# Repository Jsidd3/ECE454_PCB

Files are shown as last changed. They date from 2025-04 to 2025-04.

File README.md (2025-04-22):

# ECE454_PCB
PCB design files for UIC ECE 454 Team 6 Autonomous Race Car. PCB Designed by Jawwad Siddiqui

PCB will interface with the NXP FRDM-KL25Z board. Serves as the main power supply and motor controller for ECE 454 Team 6 Autonomous Race Car. Power supply consists of boost converter and linear regulator, and motor controller consists of FET Drivers. Current version is Rev. A.



Soldered using Voltera PCB Printer
WhatsApp Image 2025-04-14 at 16 43 18_f0a2d588
Designed using Altium Designer by Jawwad Siddiqui. Credit to Nico Gomez who also contributed to the Motor Controller Schematic.

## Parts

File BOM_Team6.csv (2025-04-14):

 | Bill of Materials
 |  |  |  |  |  |  | 2175 Salk Avenue
 | Project Title: | Bill of Materials for BOM Document [Motor_Controller_PowerSupply.BomDoc] |  |  |  |  | Suite 200
 | Project File Name: | Motor_Controller_PS.PrjPcb |  |  |  |  | Carlsbad, CA 92008
 | Assembly Variant: | None |  |  |  |  | USA
Part Number | Description | Designator | Manufacture | Manufacture Part Number | Supplier | Supplier Part Number | Supplier Unit Price | Quantity
DesignItemId | Description | Designator | Manufacturer 1 | Manufacturer Part Number 1 | Supplier 1 | Supplier Part Number 1 | Supplier Unit Price 1 | Quantity
LT1370CR#PBF | 12V Boost Converter | Boost Converter | Analog Devices / Linear Technology | LT1370CR#PBF | Digikey | 505-LT1370CR#PBF-ND | $19.50 | 1
CMP-2007-04425-2 | General Purpose Ceramic Capacitor, 0805, 47nF, 5%, X7R, 0.15, 50V | C1, C2 | Kyocera AVX | 08055C473JAT2A | Newark | 96M1415 | $0.03 | 2
2220Y2K00104KXRWS3 | Capacitor | C1Hall | Knowles Syfer | 2220Y1K00104KSTM01 | Digikey | 1608-2220Y1K00104KSTM01CT-ND | $4.02 | 1
C1812C472KGRACAUTO | Capacitor | C2Hall | KEMET | C1812C472KGRACAUTO | Digikey | 399-16791-1-ND | $0.78 | 1
CMP-03017-000047-1 | CAP TANT 1UF 10% 25V 1206 | C3 | KEMET | T491A105K025AT | Digikey | 399-3680-1-ND | $0.42 | 1
UWP1HR22MCL1GB | Capacitor Polarised | CL, Cp1, Cp4 | Nichicon | UWP1HR22MCL1GB | Digikey | 493-9831-1-ND | $0.63 | 3
GRM033R61C473KE84D | Capacitor | Cp2 | Murata | GRM033R61C473KE84D | Digikey | 490-7227-1-ND | $0.10 | 1
GRM033R71A472KA01D | Capacitor | Cp3 | Murata | GRM033R71A472KA01D | Digikey | 490-3192-1-ND | $0.10 | 1
8.65231E+11 | Capacitor Polarised | Cp5 | Wurth Electronics | 8.65231E+11 | Digikey | 732-8269-1-ND | $0.18 | 1
MBRD835L | Diode | Diode | ON Semiconductor | MBRD835LT4G | Digikey | MBRD835LT4GOSCT-ND | $1.01 | 1
CMP-05716-000008-1 | IC GATE DRVR HIGH-SIDE 18SOIC | FETDriver | Maxim | MAX620CWN+ | Digikey | MAX620CWN+-ND | $14.07 | 1
CMP-04776-000084-1 | CONN HEADER VERT 3POS 2.54MM | HallEffect, Servo | Molex | 90120-0763 | Digikey | WM8085-ND | $1.05 | 2
67996-416HLF | CONN HEADER 16POS .100 STR TIN | J1, J9 | Amphenol Communications Solutions | 67996-416HLF | Digikey | 609-3220-ND | $0.67 | 2
67996-420HLF | CONN HEADER 20POS .100 STR TIN | J2 | Amphenol ICC / FCI | 67996-420HLF | Digikey | 609-3221-ND | $0.71 | 1
67996-416HLF | CONN HEADER 16POS .100 STR TIN | J3, J7 |  |  | Octopart | Mouser - 649-67996-416HLF |  | 2
67996-412HLF | CONN HEADER 12POS .100 STR TIN | J4 |  |  | Octopart | Mouser - 649-67996-412HLF |  | 1
282857-2 | TERM BLOCK 2POS SIDE ENT 5.08MM | J5, Motor | TE Connectivity | 282857-2 | Digikey | A98359-ND | $2.07 | 2
67996-420HLF | CONN HEADER 20POS .100 STR TIN | J6 |  |  | Octopart | Mouser - 649-67996-420HLF |  | 1
67996-412HLF | CONN HEADER 12POS .100 STR TIN | J10 | Amphenol ICC / FCI | 67996-412HLF | Digi-Key | 609-3219-ND |  | 1
ETQ-P4M4R7KFM | Inductor | L1 | Panasonic | ETQ-P4M4R7KFM | Digikey | P124173CT-ND | $0.82 | 1
61300511121 | Connector | LineCamera | Wurth Electronics | 61300511121 | Digikey | 732-5318-ND | $0.24 | 1
CMP-04962-000068-1 | MOSFET N-CH 30V 24A/100A 8VSON | Q1, Q2 | Texas Instruments | CSD17306Q5A | Digikey | 296-25856-1-ND | $1.70 | 2
CMP-07231-003873-1 | Thick Film Chip Resistors 0805 10kΩ 0.125W 5% 200ppm/°C | R1, R2, R3, R4, R5 | Bourns | CR0805-JW-103ELF | Digikey | CR0805-JW-103ELFCT-ND | $0.02 | 5
LM2940IMPX-5.0_NOPB | Integrated Circuit | Regulator | TI National Semiconductor | LM2940IMPX-5.0/NOPB | Digikey | LM2940IMPX-5.0/NOPBCT-ND | $1.63 | 1
RC0402JR-0710KL | Resistor | RHall | Yageo | RC0402JR-0710KL | Digikey | 311-10KJRDKR-ND | $0.10 | 1
ERJ-2RKF5902X | Resistor | Rp1 | Panasonic | ERJ-2RKF5902X | Digikey | P59.0KLCT-ND | $0.10 | 1
RC0603FR-106K8L | Resistor | Rp2 | Yageo | RC0603FR-106K8L | Digikey | 13-RC0603FR-106K8LCT-ND | $0.10 | 1
ERJ-2RKF2001X | Resistor | Rp3 | Panasonic | ERJ-2RKF2001X | Digikey | P2.00KLDKR-ND | $0.10 | 1
 |  |  |  |  |  |  | $50.16 | 40
Approved |  | Notes

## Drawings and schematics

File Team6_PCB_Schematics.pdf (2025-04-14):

1

2

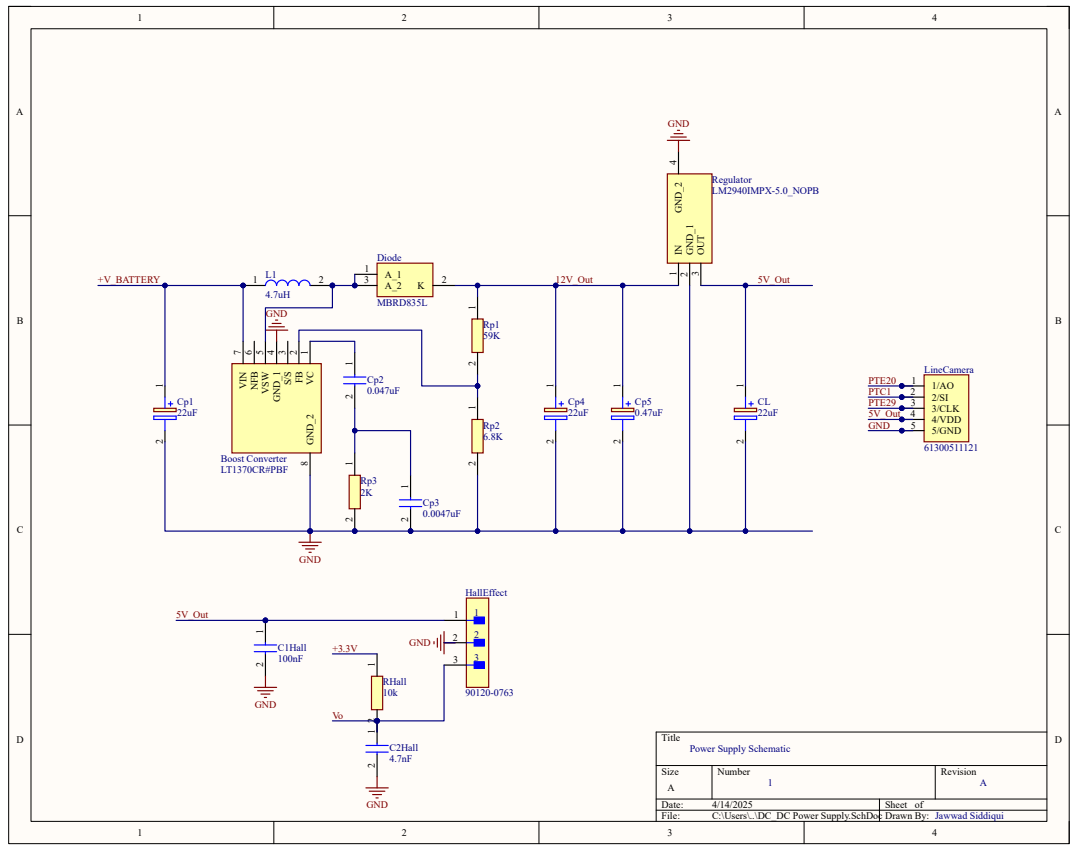
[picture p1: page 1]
Size; Number; Revision; Date:; Sheet of; File:; C:\Users\..\DC_DC Power Supply.SchDoc Drawn By: VC; 3 GND_1; 4 VSW; 5 NFB; 6 VIN; 7 GND_2; Boost Converter; LT1370CR#PBF; 1 GND_1; 2 OUT; 3 GND_2; Regulator LM2940IMPX-5.0_NOPB; GND; 12V_Out; +V_BATTERY; 5V_Out; PTE29; PTC1; PTE20; HallEffect; C2Hall 4.7nF; C1Hall; RHall 10k; GND +3.3V; Diode; MBRD835L; 1/AO 1 2/SI 2 3/CLK 3 4/VDD 4 5/GND 5; LineCamera; Jawwad Siddiqui

Title
Power Supply Schematic

1

2

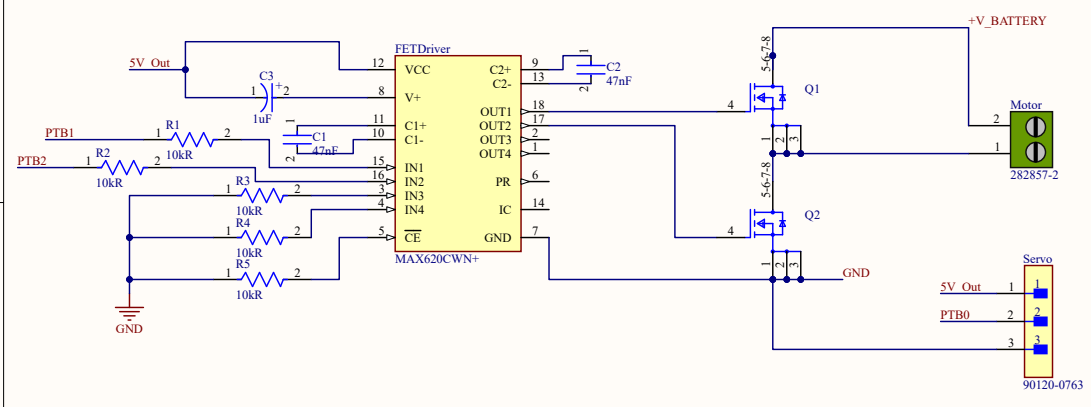
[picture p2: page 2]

Jawwad Siddiqui & Nico Gomez

# BATTERY IN

# Freedom Board Interface

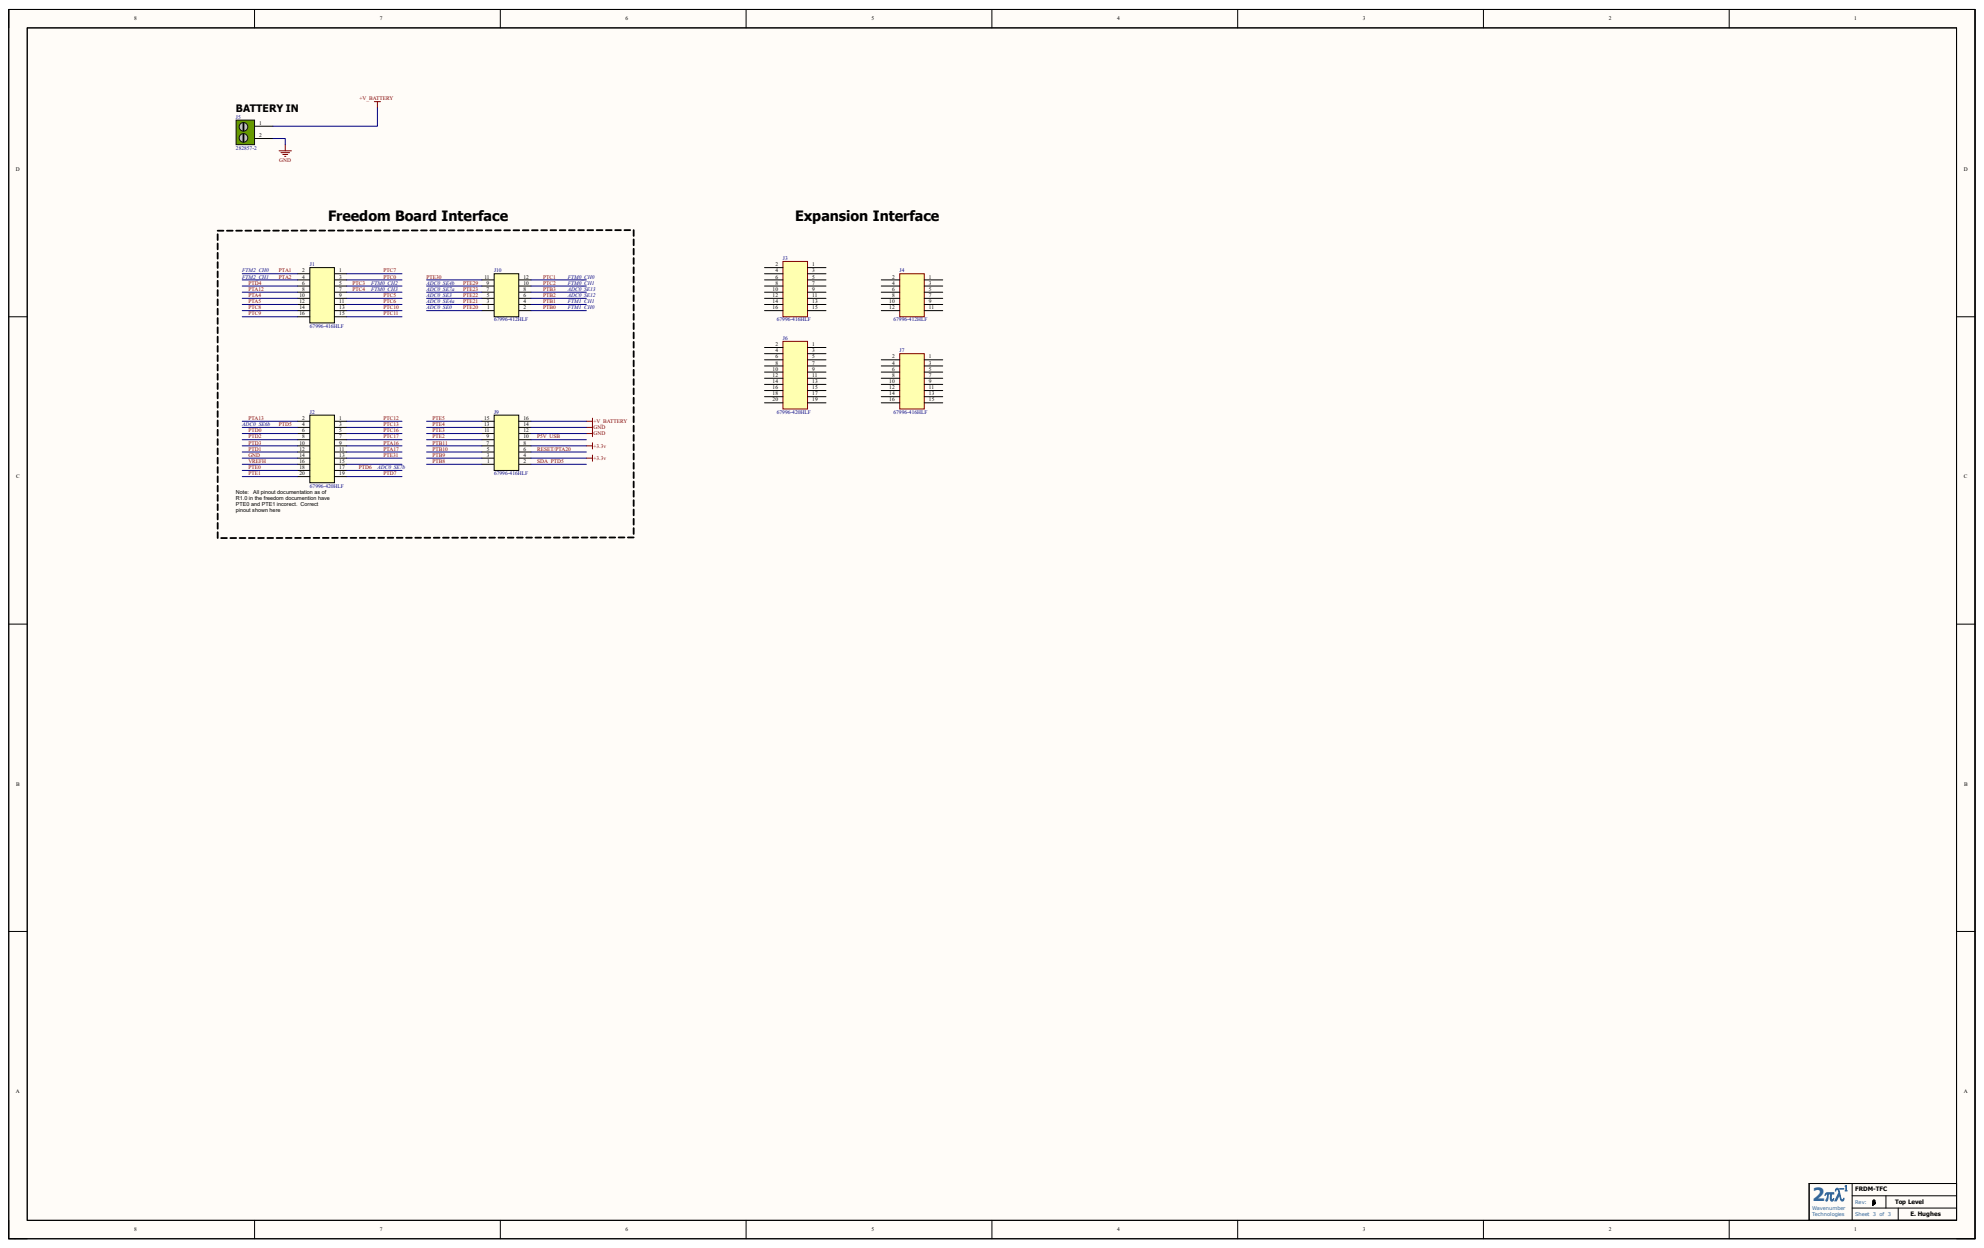
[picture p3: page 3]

Note: All pinout documentation as of
R1.0 in the freedom documention have
PTE0 and PTE1 incorect. Correct
pinout shown here

2pl⁻¹ Wavenumber Technologies | FRDM-TFC

Rev: b | Top Level

Sheet 3 3 of | E. Hughes
